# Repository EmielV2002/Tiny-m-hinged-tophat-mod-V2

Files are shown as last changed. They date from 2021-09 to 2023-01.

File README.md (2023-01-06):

# Tiny-m-hinged-tophat-mod
A mod that allows you to use a tophat with a hinge on your Tiny-m.


**Introduction:**
Hi! Welcome and thank you for choosing my Tiny-m tophat design. Before we start, I must warn you. This design has not been fully tested yet so I can’t guarantee that everything will work as it should. But I’m pretty confident it will because the test prints I made looked promising. If you’ve got questions about the design and BOM you can find me on the CroXY discord server in the Tiny-m channel. Have fun and good luck with your build ; )  

**Bill Of Materials (BOM):**

**Note:**
In the printed parts tab you can find two stl's called corner 1 without rod and corner 2 without rod. You can print these parts in one piece instead of the usual two pieces. Because you can print these as one piece you don't need those steel rods and epoxy any longer. A special thanks to Discord user nehiLo for making this remix.

**Hardware:**
-	4x 5x58mm steel rod (length doesn’t need to be that precise)
-	2x Southco E6-10-301-20 constant torque hinges (printed ones will probably work as well)
-	1 tube epoxy to glue the steel rods into place. 

**Panels:**
-	1x back panel (150 and 190mm versions available)
-	2x side panel 1 (150 and 190mm versions available)
-	2x side panel 2 (150 and 190mm versions available)
-	1x top panel (150 and 190mm versions available)

**Fasteners:**
-	8x   M5x8 BHSC for mounting the hinges to the tophat and hinge body.
-	20x M3x10 or 12mm BHSC for mounting the corner pieces and middle pieces.
-	20x M3 threaded inserts.
-	8x   M5 T-nuts.
-	6x   M5x10 BHSC for mounting the left and right hinge bodies and the panel clips.
-	2x   M5x26 BHSC for mounting the left and right hinges bodies.

**Printed parts:**

**Top half:**
-	1x corner 1 top
-	1x corner 2 top
-	1x corner 1 bottom
-	1x corner 2 bottom
-	2x middle 1
-	2x middle 2
-	8x midclip 1
-	2x cornerclip 1
-	2x cornerclip 2

**Bottom half:**
-	1x right hinge part frame
-	1x left hinge part frame
-	1x back_panel_mount – corner_left_3.5mm
-	1x back_panel_mount – corner_right_3.5mm

**Assembly guide:**



**Part 1: tophat**

Step 1: place heat inserts in the holes of corner 1 v3 shortened, middle 2 v3 and middle 1 v3.
Step 2: Using two midclip 1 clips connect corner 1 v3 shortened to middle 2 v3 and middle 1 v3.


 
Step 3: Place heat inserts in corner 2 v3 shortened and in middle 2 v3.
Step 4: Connect corner 2 v3 shortened to middle 1 v3 using another midclip 1 clip. 
Step 5: Connect corner 2 v3 shortened to middle 2 v3 using another midclip 1 clip.  



Step 6: Use epoxy or another glue to glue the metal rods in corner 1 v3 back top and corner 2 v3 back top.


 
Step 7: Put glue in the holes of corner 1 v3 bottom and corner 2 v3 bottom and place them on corner 1 v3 back top and corner 2 v3 back top. 


 
Step 8: Put heat inserts in the holes of corner 1 v3 back top and corner 2 v3 back top just like you did with corner 1 v3 and corner 2 v3.


 
Step 9: Connect the two assembled halves together using two more midclip 1’s.   



**Part 2: panels**
Step 10: install the panels. 


 
Step 11: Install corner clip 1 on corner 2 v3 and on corner 2 back v3.


  
Step 12: Install corner clip 2 on corner 1 v3 and on corner 1 back v3.



**Part 3: Hinges**
Step 13: Using the M5x8 BHSC screws mount the hinges to the two back corners. 


 
Step 14: Mount the left hinge part frame v3 and right hinge part v3 to the back corners of the frame using two T-nuts and the M5x10 BHSC screws.


 
Step 15: Use a T-nut and a M5x26 BHSC to mount to secure the hinge part firmly to the frame. DO THIS ON BOTH SIDES!



**Part 4: back panel**
Step 16: Slide the back panel in the dedicated slots in the left and right hinge parts you just installed.


 
Step 17: Lock the panel in place by screwing the back_panel_mount – corner_right_3.5mm and back_panel_mount – corner_left_3.5mm in place. Use the remaining M5x10 BHSC screws and T-nuts.



**Part 5: final assembly**
Step 18: Using the remaining M5x8 BHSC screws screw the hinges on the left and right corner parts. 



**Overview:**



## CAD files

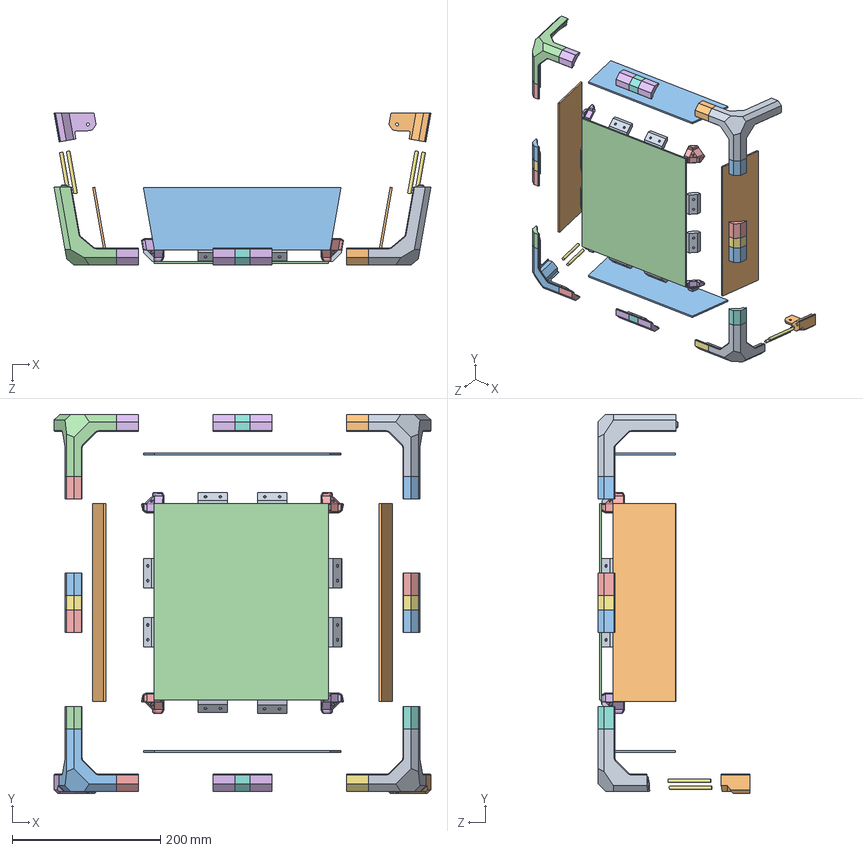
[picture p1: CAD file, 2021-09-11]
assemblies/150 mm/tophat hinge 150mm V3.SLDASM
508.0 x 511.0 x 205.1 mm
corner 2 V3 150mm
corner 2 V3 connection block 150mm
corner 2 V3 connection block 2 150mm x 3
corner 1 V3 150mm
corner 1 V3 connection block 2 150mm x 3
corner 1 connection block V3 150mm x 5
middle piece part 2 V3 150mm x 2
middle piece part 1 V3 150mm x 2
midclip 1 2x.step x 8
side panel 1.step x 2
side panel 2.step x 2
top panel.step
corner clip 1 2x.step x 2
corner clip 2 2x 150mm.step x 2
corner 1 back connection block V3 150mm
corner 1 back connection block 2 V3 150mm
corner 1 back V3 150mm top
corner 1 back V3 150mm bottom
corner 2 back V3 150mm top
corner 2 back connection block 2 V3 150mm
corner 2 back connection block V3 150mm
corner 2 back V3 150mm bottom
steel rod x 4

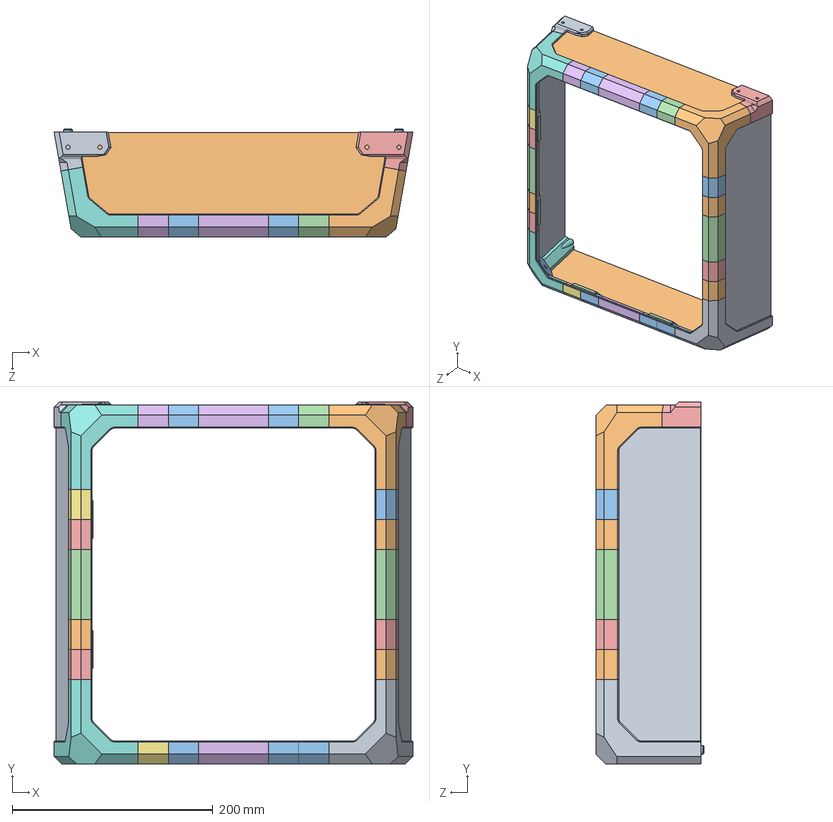
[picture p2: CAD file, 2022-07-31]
assemblies/190 mm/tophat hinge 190mm.SLDASM
358.0 x 361.0 x 108.0 mm
corner 1 2x shortened 190mm
corner 1 2x connection block 2 190mm x 3
corner 1 connection block 190mm x 5
middle piece part 2 190mm x 2
corner 2 2x connection block 2 190mm x 3
middle piece part 1 190mm x 2
corner 2 2x connection block 190mm
corner 2 2x shortened 190mm
side panel 1 190mm x 2
side panel 2 190mm x 2
corner clip 1 4x 190mm.step x 2
midclip 1 2x 190mm.step x 8
corner clip 2 2x 190mm.step x 2
corner 1 back connection block V3 150mm
corner 1 back connection block 2 V3 150mm
corner 1 back V3 150mm top
corner 1 back V3 150mm bottom
corner 2 back V3 150mm top
corner 2 back connection block 2 V3 150mm
corner 2 back connection block V3 150mm
corner 2 back V3 150mm bottom

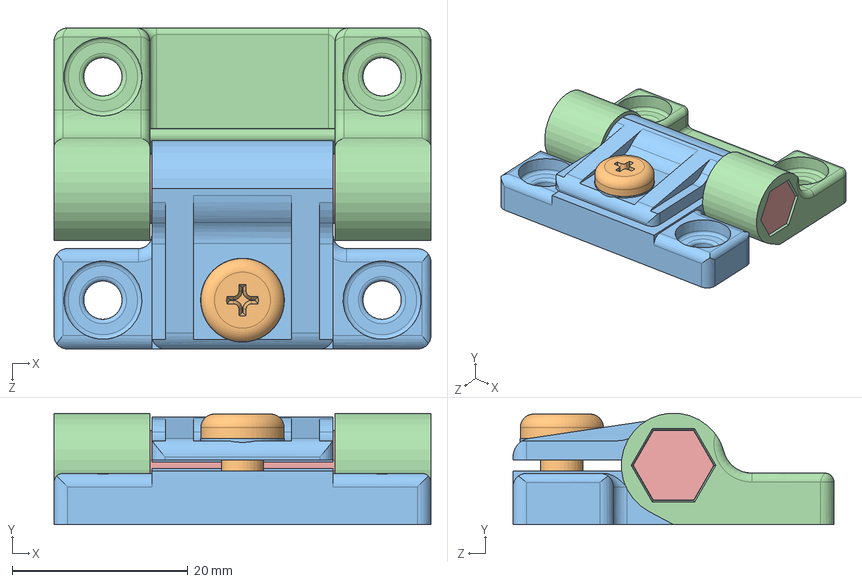
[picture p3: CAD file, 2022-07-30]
Southco-E6-10-301-20/Southco-E6-10-301-20.sldasm
42.9 x 12.7 x 36.5 mm
Southco-E6-10-301-20_E6_300_SERIES_ADJUSTMENT_NUT_FREE_RUNNING_CLF
Southco-E6-10-301-20_E6_STANDARD_PAN_HEAD_SCREW_CLF
Southco-E6-10-301-20_E6_300_SERIES_HINGE_LEAF_ADJUSTABLE_CLF
Southco-E6-10-301-20_E6_FIXED_HINGE_LEAF_CLF
Southco-E6-10-301-20_E6_HINGE_PIN_CLF

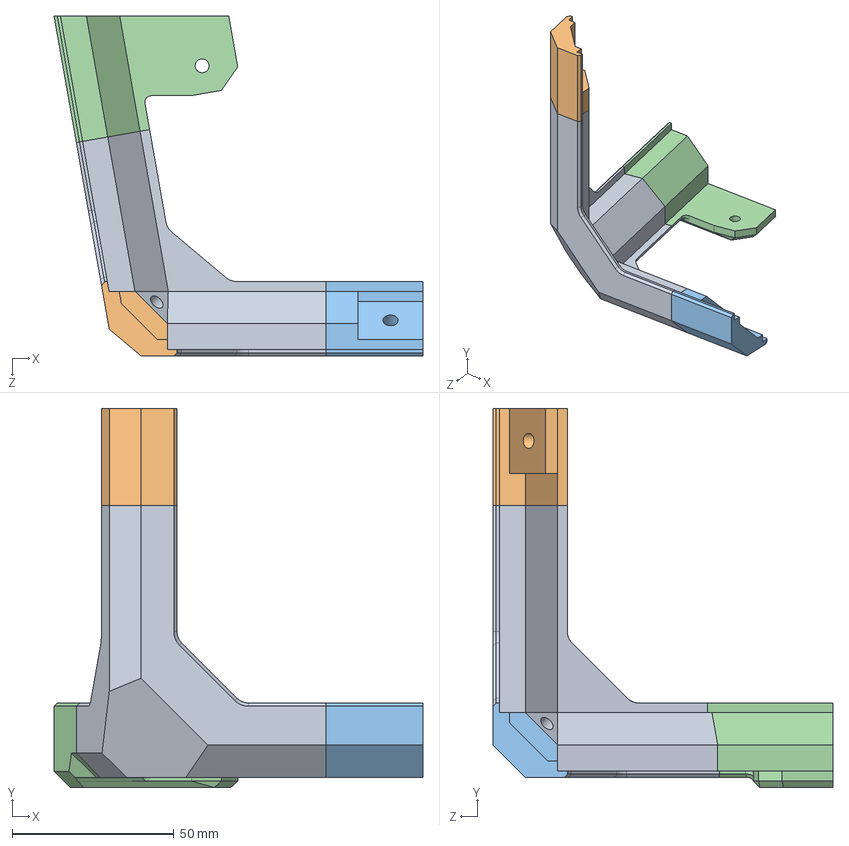
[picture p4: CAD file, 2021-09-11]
printed parts/back corners/corner 2/corner 2 back V3.SLDASM
114.0 x 117.1 x 105.1 mm
corner 2 back V3 150mm top
corner 2 back connection block 2 V3 150mm
corner 2 back connection block V3 150mm
corner 2 back V3 150mm bottom

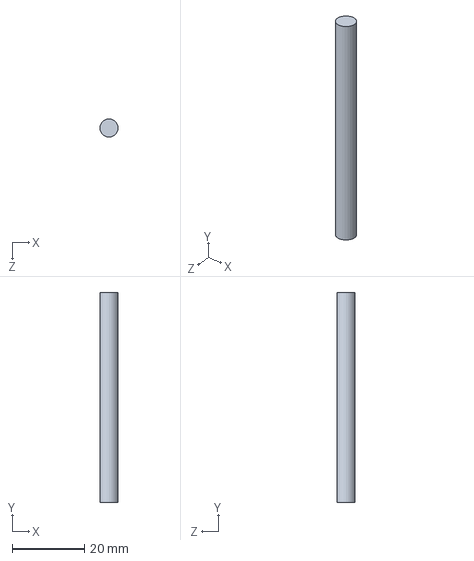
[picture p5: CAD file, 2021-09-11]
assemblies/files/steel rod.SLDPRT
5.00 x 58.0 x 5.00 mm

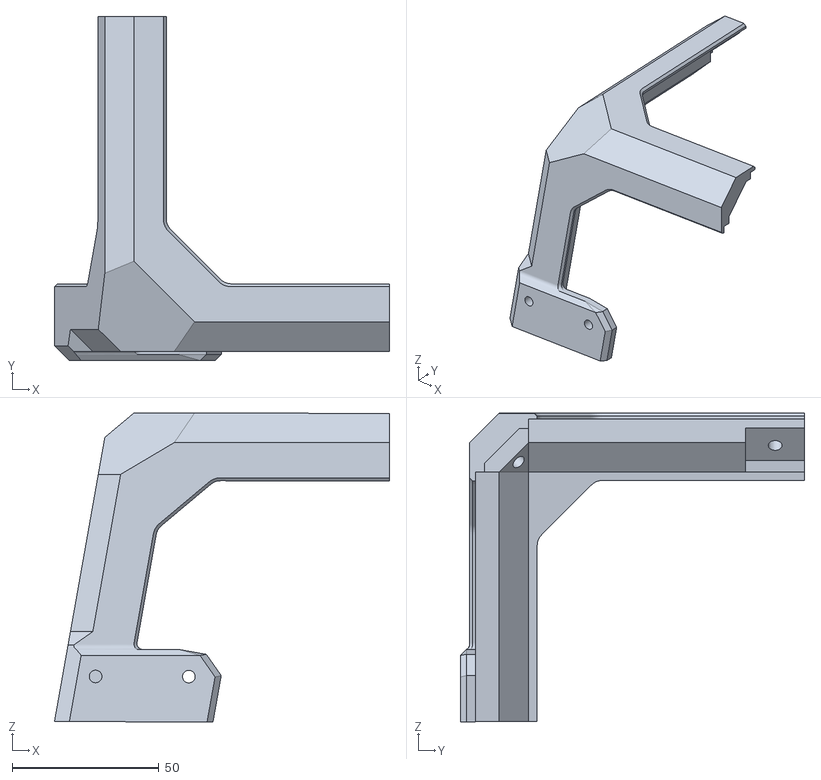
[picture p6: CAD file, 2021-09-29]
printed parts/back corners/corner 1/corner 1 without rod.stl
114.1 x 117.1 x 105.1

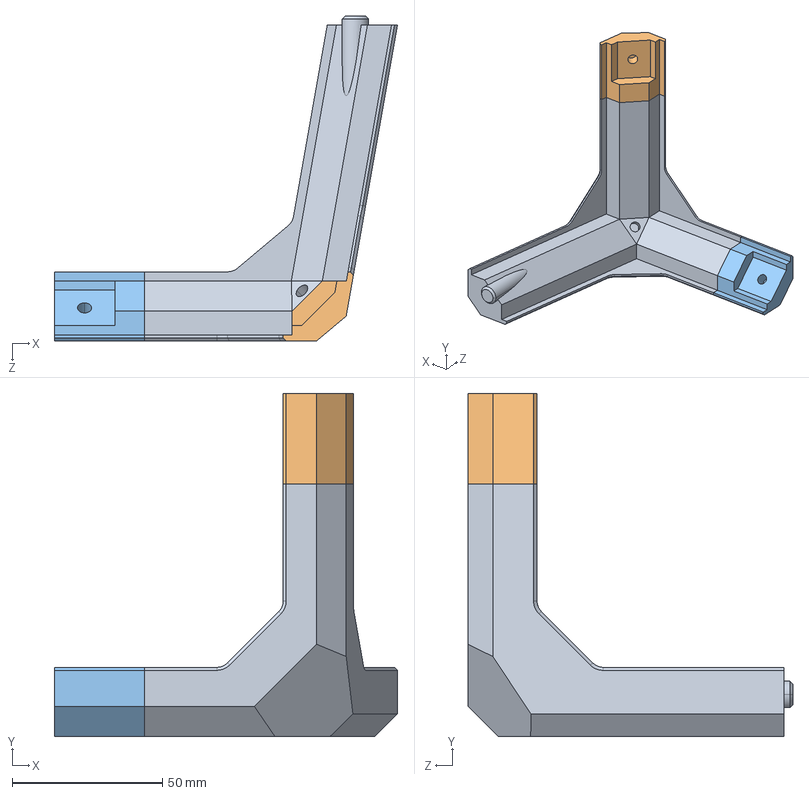
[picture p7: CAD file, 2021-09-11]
printed parts/front corners/corner 1/corner 1 V3 shortened.STEP
114.0 x 114.0 x 108.0 mm

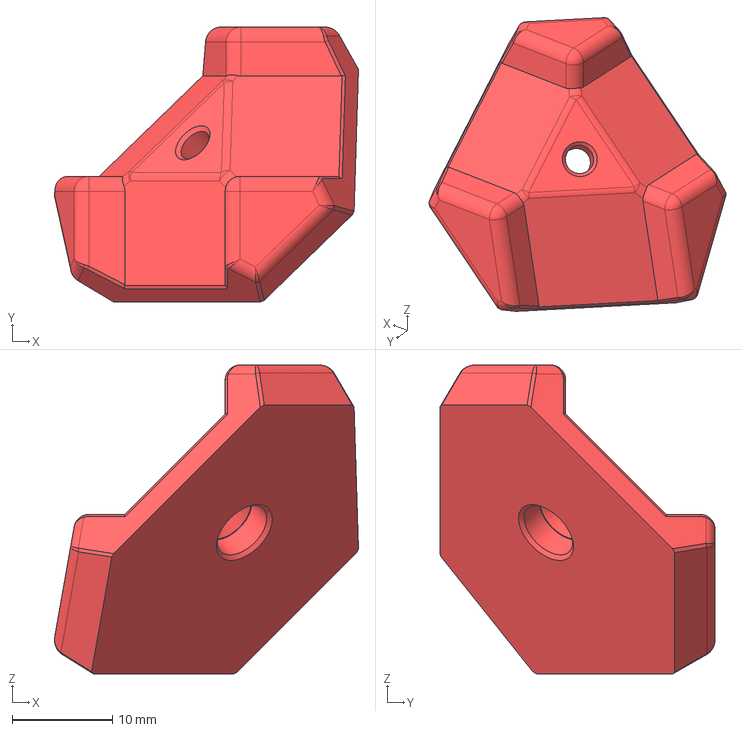
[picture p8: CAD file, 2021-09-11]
printed parts/front corners/corner clip 2 V3.step
30.3 x 27.5 x 30.8 mm

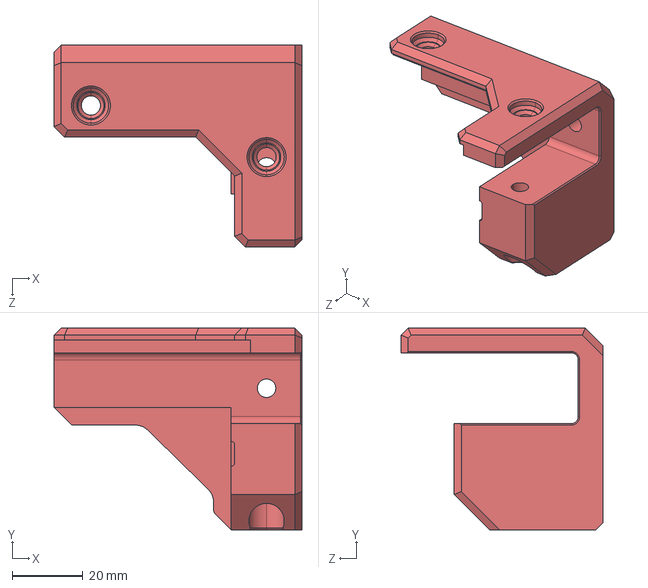
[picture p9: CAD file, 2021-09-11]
printed parts/hinge base/left hinge/left hinge part frame V3.STEP
70.0 x 57.0 x 57.0 mm

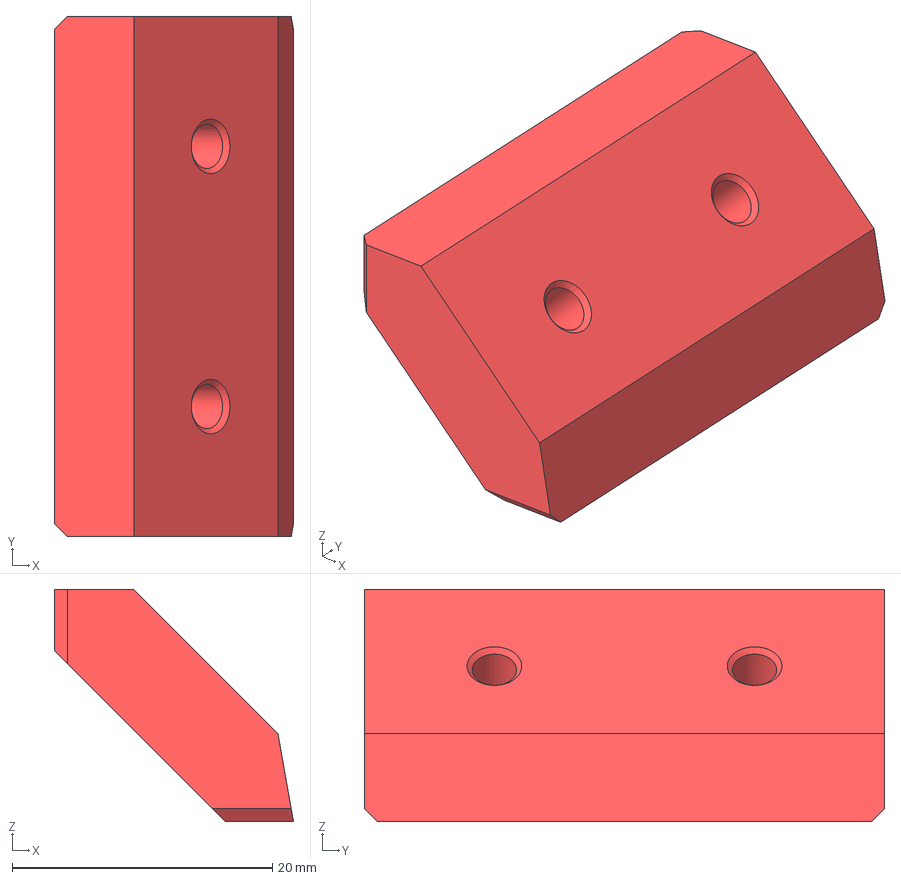
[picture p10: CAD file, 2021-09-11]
printed parts/middle connecting pieces/midclip 1 V3.step
18.4 x 40.0 x 17.9 mm

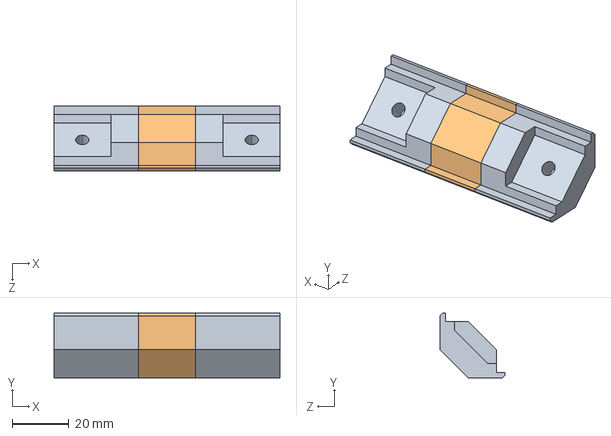
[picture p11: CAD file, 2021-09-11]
printed parts/middle connecting pieces/middle connecting pieces 150mm/middle part 1/middle 1 V3 150mm.STEP
80.0 x 23.0 x 23.0 mm

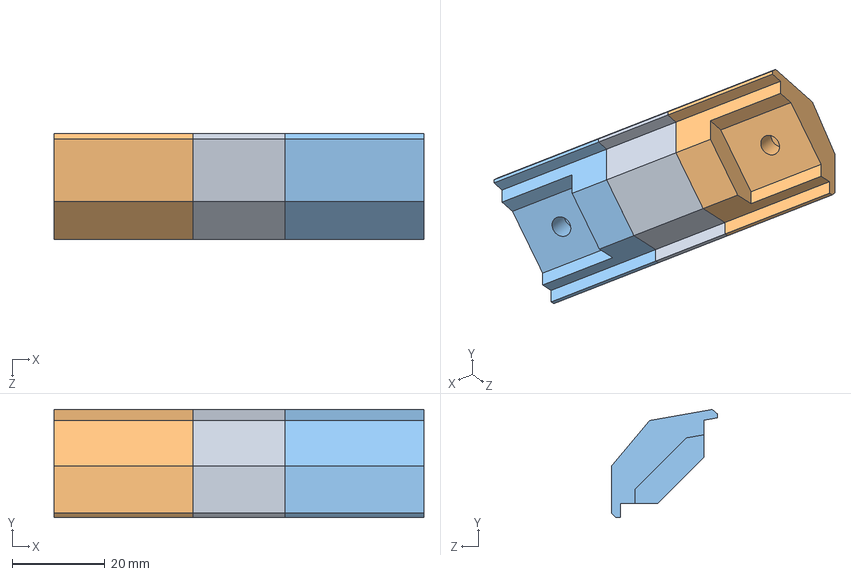
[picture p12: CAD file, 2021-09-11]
printed parts/middle connecting pieces/middle connecting pieces 150mm/middle part 2/middle 2 V3 150mm.STEP
79.9 x 23.3 x 23.0 mm

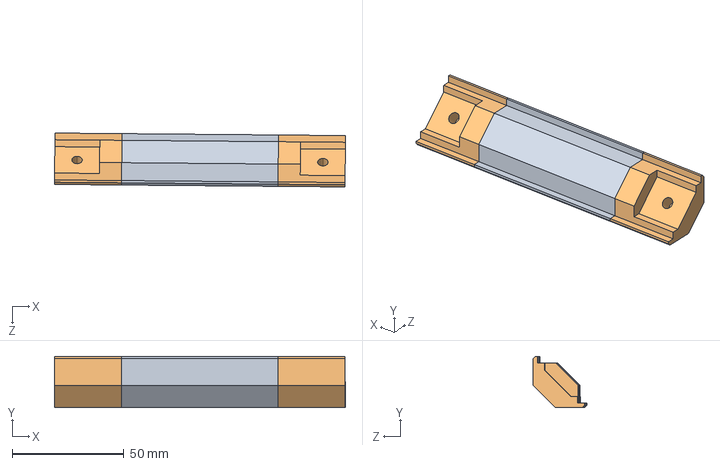
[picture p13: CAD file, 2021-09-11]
printed parts/middle connecting pieces/middle connecting pieces 190mm/middle 1/middle 1 190mm.STEP
130.2 x 23.0 x 24.1 mm
middle piece part 1 190mm
corner 1 connection block 190mm x 2

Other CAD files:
printed parts/back corners/corner 1/corner 1 back V3.SLDASM
printed parts/back corners/corner 2/corner 2 without rod.stl
printed parts/front corners/corner 2/corner 2 V3 shortened.STEP
printed parts/hinge base/right hinge/right hinge part frame V3.STEP
printed parts/middle connecting pieces/middle connecting pieces 190mm/middle 2/middle 2 190mm.STEP
Southco-E6-10-301-20/Southco-E6-10-301-20 - Southco-E6-10-301-20_E6_300_SERIES_ADJUSTMENT_NUT_FREE_RUNNING_CLF-1.STL
Southco-E6-10-301-20/Southco-E6-10-301-20 - Southco-E6-10-301-20_E6_300_SERIES_HINGE_LEAF_ADJUSTABLE_CLF-1.STL
Southco-E6-10-301-20/Southco-E6-10-301-20 - Southco-E6-10-301-20_E6_FIXED_HINGE_LEAF_CLF-1.STL
Southco-E6-10-301-20/Southco-E6-10-301-20 - Southco-E6-10-301-20_E6_HINGE_PIN_CLF-1.STL
Southco-E6-10-301-20/Southco-E6-10-301-20 - Southco-E6-10-301-20_E6_STANDARD_PAN_HEAD_SCREW_CLF-1.STL
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

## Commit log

2021-09-11 all updated files
    [Southco-E6-10-301-20 - Southco-E6-10-301-20_E6_300_SERIES_ADJUSTMENT_NUT_FREE_RUNNING_CLF-1.STL, Southco-E6-10-301-20 - Southco-E6-10-301-20_E6_300_SERIES_HING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]
2021-09-29 corners without rods
    This update allows you to print the corener pieces as one piece. Because of thise you won't be needing the steel rods or epoxy anylonger.
    [corner 1 without rod.stl, corner 2 without rod.stl]
2022-07-30 Update
    Updated file paths. May or may not have to retry this.
    [Southco-E6-10-301-20.sldasm, Southco-E6-10-301-20_E6_300_SERIES_ADJUSTMENT_NUT_FREE_RUNNING_CLF.sldprt, Southco-E6-10-301-20_E6_300_SERIES_HINGE_LEAF_ADJUSTABL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]
2022-07-31 Add step files
    assembly step files have been added
    [tophat hinge 190mm.SLDASM]
